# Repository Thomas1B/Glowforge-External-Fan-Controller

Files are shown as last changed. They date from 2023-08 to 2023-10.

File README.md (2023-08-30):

# Glowforge External Fan Controller

**Note: This will avoid any warranty of glowforge**

This program is designed to read the voltage from the fan pin on the Glowforge laser cutter. When the pin is high, a relay is turned on to run an exhaust fan. After the voltage drops back to 0, the fan runs for a little longer to allow for better exhaust of fumes.

## Components

To make the controller the following components are needed:<br>
1. Attiny85.
2. 5V Regulator.
3. AC Relay, with activation voltage of 3.3V or 5V.
4. Red led.
5. Green led.
6. 10K Resistor.
7. 2 x Resistor for LEDs (depends on brightness).
8. Diode.
9. 10uF Capacitor.
10. 22uF Capacitor.
11. Momentary Push Button.
12. Slide Switch.
13. Terminal Block.
14. JST Connector.
15. Pin Headers.

Also needed is some arduino board to program the attiny85.

DigiKey (https://www.digikey.ca/) is a great place to buy electronics from.

The attiny85 is very small microcontroller, convienent for simple projects. The AC relay is used to run an external exhaust fan when the controller senses high voltage. The red led is used to notify that the controller has power, and the green is show that relay should be running (which is useful for debugging if the fan should be run and it's not). The button is used a reset and the switch is used to manually active the relay.

## Diagrams
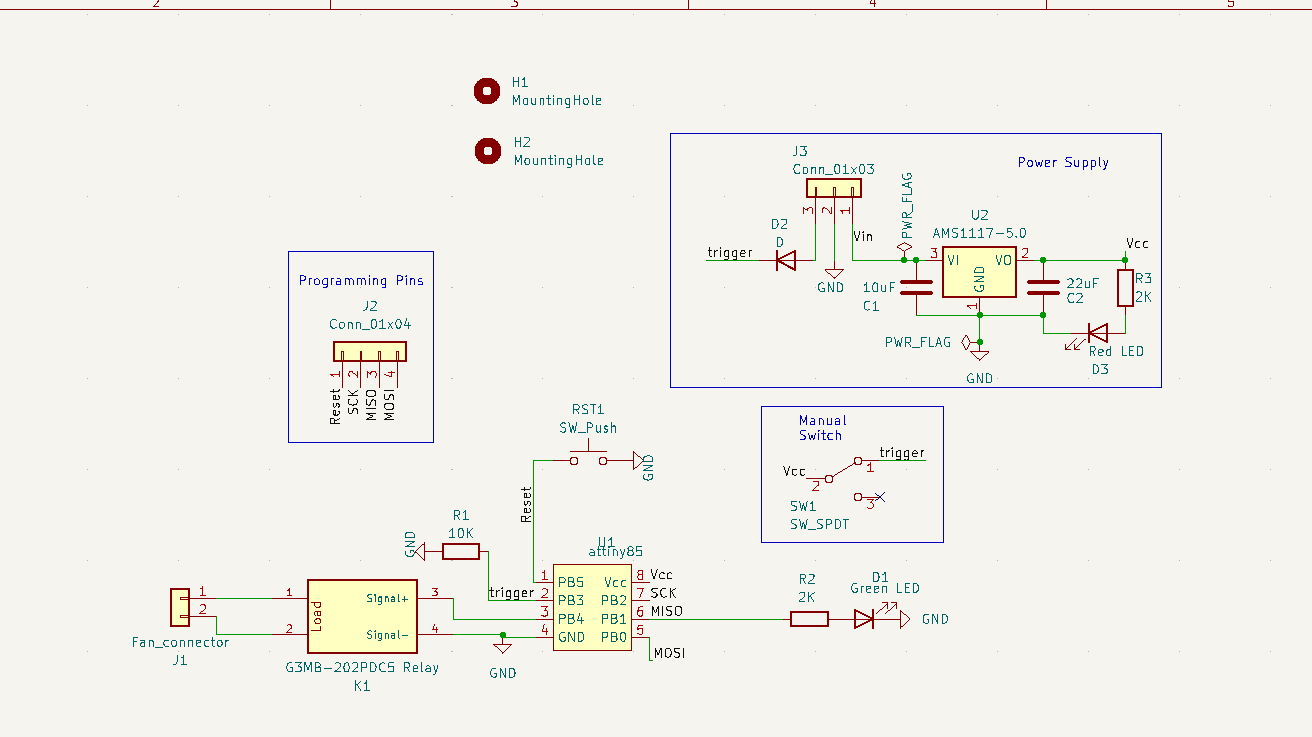
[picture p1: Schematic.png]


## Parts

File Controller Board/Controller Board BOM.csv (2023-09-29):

"Project:","Controller Board\Controller Board.kicad_sch"
"Date:","9/28/2023"
"Tool:","Eeschema 7.0.6"
"BOM Generator:","myScripts\myKiCad_BOM_Maker.py"
"Total Component Count:","18"
"Component Type Count:","16"
"Ref","Qnty","Value","Description","Cmp name","Footprint"
"Component: 1/16:"
"C1","1","10uF","Unpolarized capacitor","C","Capacitor_SMD:C_0805_2012Metric_Pad1.18x1.45mm_HandSolder"
"Component: 2/16:"
"C2","1","22uF","Unpolarized capacitor","C","Capacitor_SMD:C_0805_2012Metric_Pad1.18x1.45mm_HandSolder"
"Component: 3/16:"
"D1","1","Green LED","Light emitting diode","LED","LED_SMD:LED_0805_2012Metric_Pad1.15x1.40mm_HandSolder"
"Component: 4/16:"
"D2","1","D","Diode","D","0_Thomas_Footprints:Diode-SOD-80"
"Component: 5/16:"
"D3","1","Red LED","Light emitting diode","LED","LED_SMD:LED_0805_2012Metric_Pad1.15x1.40mm_HandSolder"
"Component: 6/16:"
"H1, H2","2","MountingHole","Mounting Hole without connection","MountingHole","MountingHole:MountingHole_3.2mm_M3"
"Component: 7/16:"
"J1","1","Fan_connector","Generic connector, single row, 01x02","Conn_01x02","0_Thomas_Footprints:myTerminalBlock-2_P5.08mm"
"Component: 8/16:"
"J2","1","Conn_01x04","Generic connector, single row, 01x04","Conn_01x04","Connector_PinHeader_2.54mm:PinHeader_1x04_P2.54mm_Vertical"
"Component: 9/16:"
"J3","1","Conn_01x03","Generic connector, single row, 01x03","Conn_01x03","Connector_JST:JST_XH_B3B-XH-A_1x03_P2.50mm_Vertical"
"Component: 10/16:"
"K1","1","AQG22105","SS Relay, 5V trig, 250AC 2A","AQG22105 Relay","0_Thomas_Footprints:RELAY_AQG22105"
"Component: 11/16:"
"R1","1","10K","Resistor","R","Resistor_SMD:R_0805_2012Metric_Pad1.20x1.40mm_HandSolder"
"Component: 12/16:"
"R2, R3","2","2K","Resistor","R","Resistor_SMD:R_0805_2012Metric_Pad1.20x1.40mm_HandSolder"
"Component: 13/16:"
"RST1","1","SW_Push","Push button switch, generic, two pins","SW_Push","0_Thomas_Footprints:SW_PTS636_SM43J_SMTR_LFS"
"Component: 14/16:"
"SW1","1","SW_SPDT","Switch, single pole double throw","SW_SPDT","0_Thomas_Footprints:EG1218 Slide Switch"
"Component: 15/16:"
"U1","1","attiny85","ATtiny85","ATTINY85","Package_DIP:DIP-8_W7.62mm"
"Component: 16/16:"
"U2","1","AMS1117-5.0","1A Low Dropout regulator, positive, 5.0V fixed output, SOT-223","AMS1117-5.0","Package_TO_SOT_SMD:SOT-223-3_TabPin2"

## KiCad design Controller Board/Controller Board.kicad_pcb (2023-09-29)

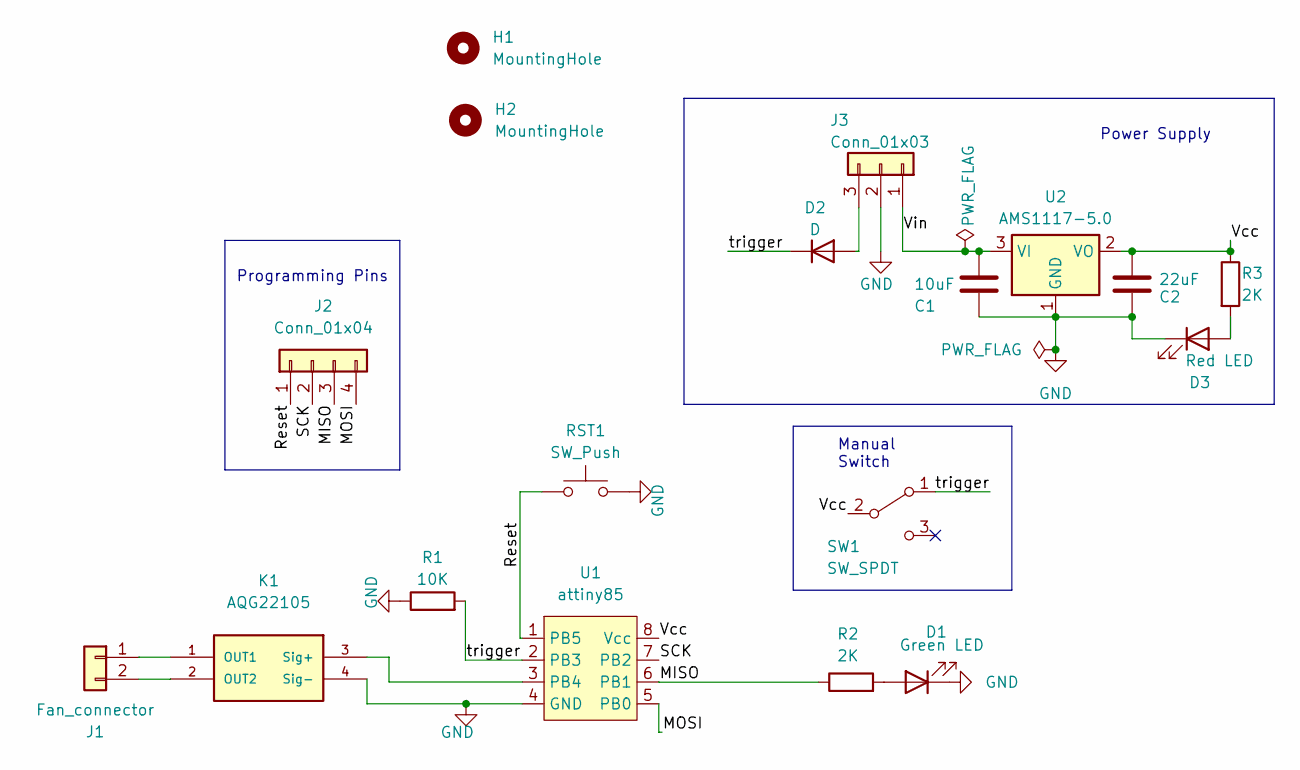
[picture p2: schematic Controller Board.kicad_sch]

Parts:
C1: 10uF; C_0805_2012Metric_Pad1.18x1.45mm_HandSolder
C2: 22uF; C_0805_2012Metric_Pad1.18x1.45mm_HandSolder
D1: Green LED; LED_0805_2012Metric_Pad1.15x1.40mm_HandSolder
D2: D; Diode-SOD-80
D3: Red LED; LED_0805_2012Metric_Pad1.15x1.40mm_HandSolder
H1, H2: MountingHole; MountingHole_3.2mm_M3
J1: Fan_connector; myTerminalBlock-2_P5.08mm
J2: Conn_01x04; PinHeader_1x04_P2.54mm_Vertical
J3: Conn_01x03; JST_XH_B3B-XH-A_1x03_P2.50mm_Vertical
K1: AQG22105; RELAY_AQG22105
R1: 10K; R_0805_2012Metric_Pad1.20x1.40mm_HandSolder
R2, R3: 2K; R_0805_2012Metric_Pad1.20x1.40mm_HandSolder
RST1: SW_Push; SW_PTS636_SM43J_SMTR_LFS
SW1: SW_SPDT; EG1218 Slide Switch
U1: attiny85; DIP-8_W7.62mm
U2: AMS1117-5.0; SOT-223-3_TabPin2

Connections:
/MISO: J2.3, R2.1, U1.6 (PB1)
/MOSI: J2.4, U1.5 (PB0)
/Reset: J2.1, RST1.2, U1.1 (PB5)
/SCK: J2.2, U1.7 (PB2)
/Vcc: C2.2, R3.1, SW1.2 (B), U1.8 (Vcc), U2.2 (VO)
/Vin: C1.2, J3.1, U2.3 (VI)
/trigger: D2.1 (K), R1.2, SW1.1 (A), U1.2 (PB3)
GND: C1.1, C2.1, D1.1 (K), D3.1 (K), J3.2, K1.4 (Sig-), R1.1, RST1.1, U1.4 (GND), U2.1 (GND)
unnamed: D1.2 (A), R2.2
unnamed: D2.2 (A), J3.3
unnamed: D3.2 (A), R3.2
unnamed: J1.1, K1.1 (OUT1)
unnamed: J1.2, K1.2 (OUT2)
unnamed: K1.3 (Sig+), U1.3 (PB4)

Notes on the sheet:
Power Supply
Manual Switch
Programming Pins

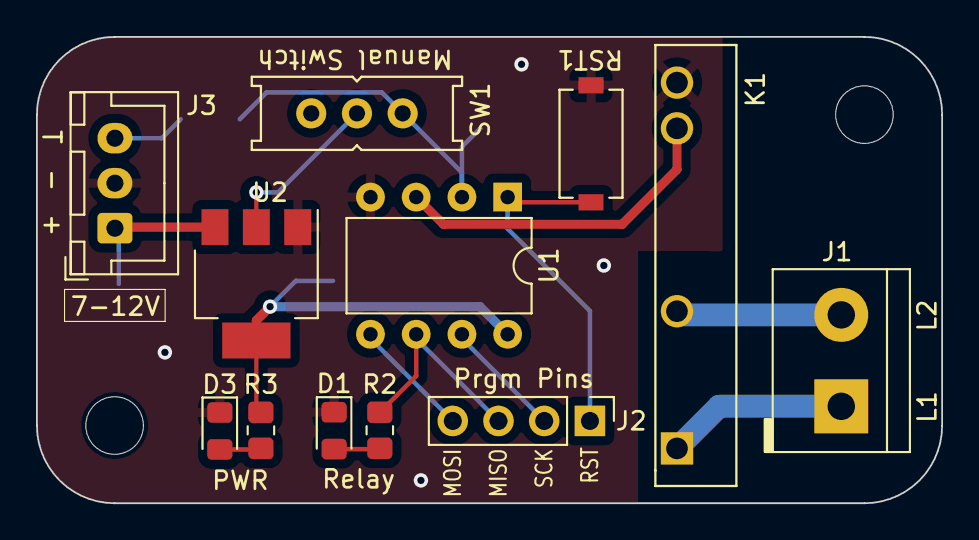
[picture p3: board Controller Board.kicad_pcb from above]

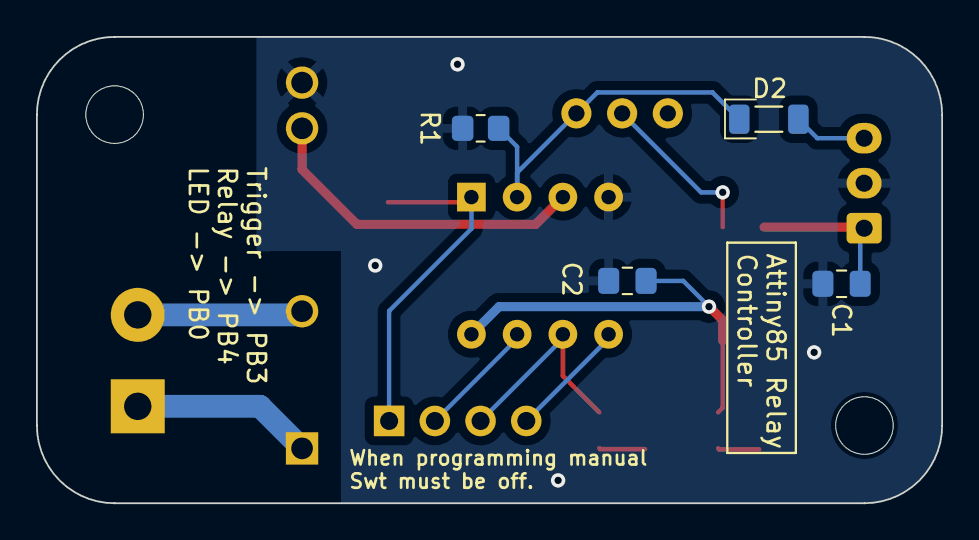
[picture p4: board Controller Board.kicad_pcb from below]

Board: 2 copper layers, 50.3 x 25.9 mm, 18 parts (4 on the bottom side), 14 nets.

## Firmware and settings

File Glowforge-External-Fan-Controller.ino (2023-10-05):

/* 
This program is designed using an ATTiny85 to sense when voltage is high on the
glowforge laser cutter fan pin. If it is high, then using a relay an external exhaust fan will turn on.

*/

// ******************* Variables user can change *******************
// Note: depending on pins used, digitalRead and analogRead may have to be switch in the lower functions, recommend not to change.

// Defining pins: (see Datasheet for pinouts: https://ww1.microchip.com/downloads/en/devicedoc/atmel-2586-avr-8-bit-microcontroller-attiny25-attiny45-attiny85_datasheet.pdf)
const int powerState_led_pin = 1;  // Led to nofity about power state (green led).
const int fan_pin = 3;             // trigger pin externally connected top fan pin on Glowforge.
const int relay_pin = 4;           // pin to power relay.

// extra time to run the fan after the voltage drops back to 0.
// this is not exact time due to run time of the program.
const int extra_run_time = (1000 / 1) * 15;  // (1000 millis / 1 secs) * X secs


// ******************* DO NOT CHANGE ANYTHING PAST HERE *******************

// Global variables
bool relay_state = false;          // if relay is on or off.
unsigned long last_high_time = 0;  // last time voltage was high.

// Other variables
unsigned long TimeOfLastDebounce = 0;
const long DebounceTime = 0.01;


// ************* Functions *************

void run_led(int pin, bool state = false) {
  /*
  Function to run the led.

    Parameters:
      pin: pin to led.
      state: true - on, false - off.
  */
  digitalWrite(pin, state);
}


void run_relay(int pin, bool state = false) {
  /* 
    Function to run the relay

      Parameters:
        pin: pin to relay.
        state: power state of relay, true - on, false - off.
  */

  if (state) {
    analogWrite(pin, 255);
    run_led(powerState_led_pin, true);
  } else {
    analogWrite(pin, 0);
    run_led(powerState_led_pin, false);
  }
}


// ************* Main Program *************


void setup() {
  /* Set up function to initialize things */
  pinMode(powerState_led_pin, OUTPUT);
  pinMode(relay_pin, OUTPUT);
  pinMode(fan_pin, INPUT);

  // flashing led for start up.
  for (int i = 0; i < 10; i++) {
    run_led(powerState_led_pin, false);
    delay(50);
    run_led(powerState_led_pin, true);
    delay(50);
  }
  run_led(powerState_led_pin, false);
}

void loop() {
  /* Main Loop */

  if ((millis() - TimeOfLastDebounce) > DebounceTime) {  // if statement for debouncing.

    bool power_state = false;

    float voltage = analogRead(fan_pin);  // reading fan pin on the glowforge.
    voltage *= (5.0 / 1023.0);            // mapping voltage
    if (voltage >= 3.0) {
      power_state = true;
    }

    if (power_state) {  // if power state is high:
      if (!relay_state) {
        // if the relay is off, then turn it on and the running light.
        relay_state = true;
        run_led(powerState_led_pin, relay_state);
        run_relay(relay_pin, relay_state);
      }
      last_high_time = millis();  // last time fan pin was read high.
    } else {
      if ((millis() - last_high_time) >= extra_run_time) {  // after the extra run time, turn off the relay and light :
        relay_state = false;
        run_led(powerState_led_pin, relay_state);
        run_relay(relay_pin, relay_state);
      }
    }
  }

  TimeOfLastDebounce = millis();  // debouncing
}

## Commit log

2023-08-23 created KiCad files
    [Fan Controller.kicad_pcb, Fan Controller.kicad_sch]
2023-08-29 updated schematic
    [Controller Board.kicad_pcb, Controller Board.kicad_sch, Fan Controller.kicad_pcb]
2023-08-30 created final Schematic and PCB
    [Controller Board.kicad_pcb]
2023-08-30 add Screenshot of schematic
2023-08-30 final verison
    [Controller Board.kicad_pcb, Controller Board.kicad_sch]
2023-09-05 final Schematic
2023-09-29 final version
    [Controller Board BOM.csv, Controller Board.kicad_pcb, Controller Board.kicad_sch]
